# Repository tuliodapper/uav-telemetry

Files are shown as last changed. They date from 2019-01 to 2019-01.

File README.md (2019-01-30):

# uav-telemetry
The purpose of this work is to provide a cost-effective method to gather important information of a flight for project validation. Because some of the data need to be gathered at a particular condition, it is desirable that the flight is constantly monitored in order to help the pilot to achieve a specified condition, e.g., altitude. To sum up, this work aims to build a platform responsible for collecting airspeed, orientation and altitude of a fixed-wing UAV flight, and current drained by the radio receiver and the servo actuators. In addition, the low-cost instrumentation system should be capable of acquiring, storing and transmitting these relevant flight parameters to a ground control station.

## Folders

### doc
Contains report, articles, presentation and video.

### software
Contains MATLAB code for the control panel interface, which aims to monitor the data collected from the acquisition board and transmitted to the ground station. Use MATLAB R2015a or later versions.

### firmware
Contains Arduino code and libraries for the firmware of the acquisition board.

### hardware
Contains the board and schematic EAGLE files for the hardware of the acquisition board.

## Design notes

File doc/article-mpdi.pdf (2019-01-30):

## drones (http://www.mdpi.com/journal/drones)

Article

# Development and Testing of a Low-Cost Instrumentation Platform for Fixed-Wing UAV Performance Analysis

Tulio Dapper e Silva ID (https://orcid.org/0000-0002-4841-0418) and Vinicius Cabreira and Edison Pignaton de Freitas *

Department of Electrical Engineering, Federal University of Rio Grande do Sul, Porto Alegre, RS 90035-190, Brazil; tuliodapper@gmail.com (T.D.e.S.); vinicius.cabreira@outlook.com (V.C.)
* Correspondence: edison.pignaton@ufrgs.br

Received: 22 April 2018; Accepted: 17 May 2018; Published: 21 May 2018

(http://www.mdpi.com/2504-446X/2/2/19?type=check_update&version=1)

Abstract: The flight data of a fixed-wing Unmanned Aerial Vehicle (UAV) can be evaluated by its designers in order to analyze its performance, to validate the project criteria and to make new decisions based on the data analyses. In this paper, the authors propose the development of a low-cost instrumentation platform capable of collecting the following data: airspeed, orientation and altitude of the airplane, and the current drained by the electric system. Moreover, this paper presents the use of a telemetry system in order to display the flight conditions to the pilot. The system contains a variety of sensors, which were chosen based on their price, applicability and ease of use. After a test flight had been performed, the collected measurements were plotted and analyzed. Having the flight data, a set of flight characteristics might be observed.

Keywords: Unmanned Aerial Vehicle; instrumentation; telemetry; flight data

### 1. Introduction

The design of an aircraft is a challenging process that requires intelligent use of aerodynamic knowledge and involves making a large number of decisions [1]. Ground-based methods, such as wind tunnels, simulators and software models, although useful, are limited in their ability to fully model the dynamic and true nature of an actual flight [2]. Moreover, Stoliker [2] points out that flight test data are essential to both improve and validate the accuracy of models and simulations.
The purpose of this work is to provide a cost-effective method to gather important information of a flight for project validation. Because some of the data need to be gathered at a particular condition, it is desirable that the flight is constantly monitored in order to help the pilot to achieve a specified condition, e.g., altitude. In addition, this study is focused on providing an affordable tool for students participating in SAE AeroDesign competition [3].
Roskam and Lan [4] and Ojha [5] point out that the airspeed, orientation, and altitude are fundamental information in order to analyze critical conditions of a flight. In a UAV, the current drained by the electric system is important to specify battery and wire sizes. Further, the current measurement could also be used to trace a relation between the torque applied to a servo and the flight control surface attached to it. To sum up, this work aims to build a platform responsible for collecting airspeed, orientation and altitude of a fixed-wing UAV flight, and current drained by the radio receiver and the servo actuators. In addition, the low-cost instrumentation system should be capable of acquiring, storing and transmitting these relevant flight parameters to a ground control station. Besides this introduction, the paper is structured as follows: Section 2 presents some related works to this paper. Section 3 discusses the requirements for each measurement. Section 4 presents the conception of the instrumentation systems, reviewing important concepts used in its development.
Drones 2018, 2, 19; doi:10.3390/drones2020019 (http://dx.doi.org/10.3390/drones2020019) | www.mdpi.com/journal/drones

Drones 2018, 2, 19 | 2 of 14

Section 5 describes and discusses the acquired results, while Section 6 concludes the paper, providing also directions for future work.

### 2. Related Works

A portable and low-cost hardware for flight testing in commercial aircraft was proposed by Kish et al. [6]. The developed instrumentation system was capable of collecting airspeed, pressure, altitude, and ambient temperature, among other measurements. The authors considered that the platform has shown promising potential to perform flight test measurements and would be useful as a primary flight reference system for home-built aircraft.
An instrumentation system might be needed for many applications and rather exclusively aircraft’s projects evaluation. For instance, Kugler and Holzapfel [7] proposed the use of flight data for implementing automatic take-off maneuver for a fixed-wing UAV and Lesprier et al. [8] presented a robust nonlinear control of a fixed-wing UAV. Moreover, Bryson and Sukkarieh [9] described the use of this information for building large-scale 3D terrain reconstructions.
In order to collect, process and store important flight data, Rodriguez et al. [10] presented an acquisition platform for experimental UAV research. The proposal was collecting UAV’s flight data (e.g., airspeed, ground speed, position, altitude, angle of attack and sideslip) focused on providing accurate and synchronized timestamps to all measurements. Complementary to those studies analyzed above, other studies (see for example [11–14]) described alternative methods of estimating attitude and position during a UAV’s flight performing data fusion algorithms.

### 3. Project Requirements’ Specification

As a starting point for this proposed work, a study about the target UAV platform was performed. Based on this study, the requirements for the desired instrumentation systems were defined. The fixed-wing UAV named “JF-01”, developed by Pampa AeroDesign UFRGS, was taken as a reference platform, which is depicted in Figure 1. Then, the desired range and accuracy of each measurement was specified to facilitate the determination of the sensors and the methods to be used.

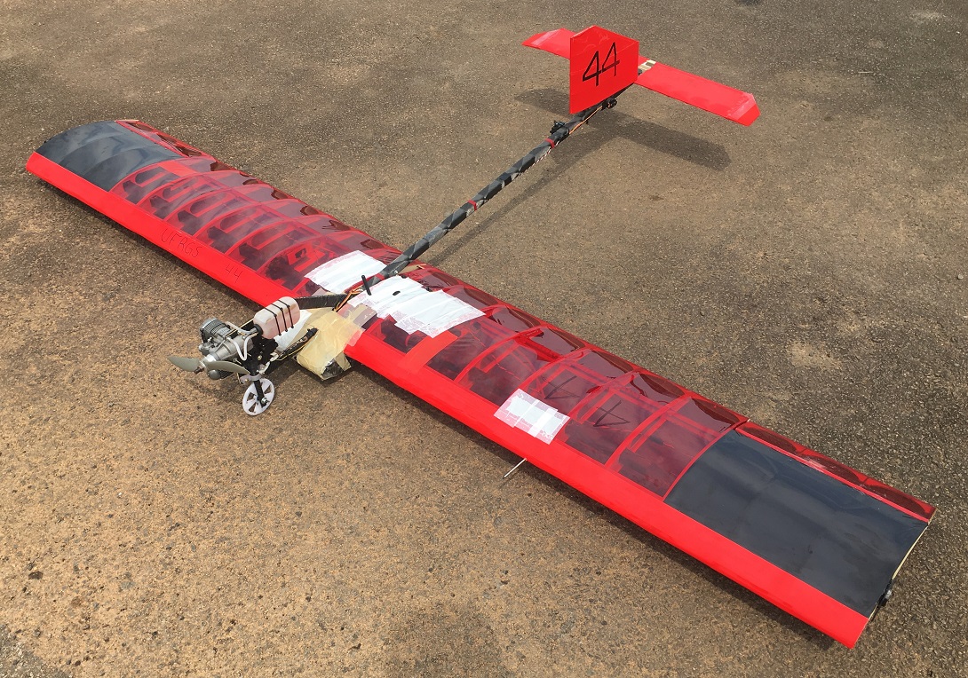
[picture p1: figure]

Figure 1. Fixed-wing UAV used as a reference to the project requirements’ specification.

Aiming to address the UAV’s requirements proposed by the SAE Aerodesign competition, the airspeed below 10 m/s is not interesting, because the airplane would not be able to carry enough load. For structural reasons, the UAV is not capable of flying over 20 m/s. Thus, the measuring range should be 10 m/s up to 20 m/s. The maximum permissible error is 0.5 m/s.
The orientation might be used to verify the rolling criteria in a fixed-wing UAV project. The JF-01 was projected to reach 30o
in 0.7 s. In order to collect at least 10 points of this movement, the sample period needs to be up to 70 ms. The maximum permissible error is 1.5o

In the flight testing location, the altitude reached by the UAV would not pass 300 m above sea level. For this measurement, the maximum permissible error is 0.5 m.
In addition, the platform should be able to measure the maximum current drawn by the electric system. The maximum permissible error is 50 mA.

### 4. Materials and Methods

As an overview, Figure 2 depicts the sensors considered in this work. As can be seen, there are six components attached to the main microcontroller: two of them are responsible for storing and transmitting the data, and the other four are sensors responsible for taking single measurements. In this section, each of these six components will be presented with a discussion of its choice instead of others available on the market.

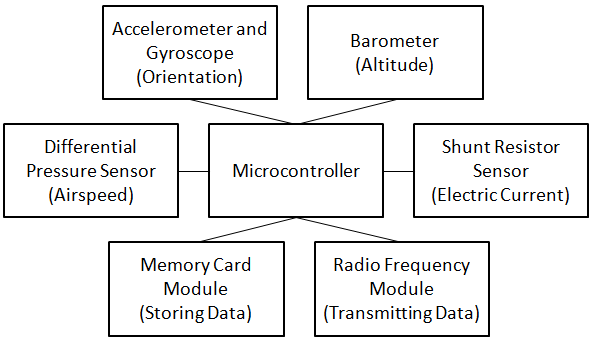
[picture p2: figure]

Figure 2. Principal components attached to the main microcontroller.

4.1. Microcontroller

In order to implement the airplane instrumentation system, an Arduino prototype platform was chosen to be used due to its low price, ease of use and ease of programming. Another important feature analyzed to decide the platform, was its size and weight, so that not too much weight had to be added to the airplane. Thus, among the available Arduino models, the Arduino Nano is a small board having similar technical specifications to the well-known Arduino Uno. Hence, the Arduino Nano was chosen.
An important parameter to be considered of the chosen platform is the quantization step size. This parameter, represented by δ, is the resolution of an analog-to-digital converter (ADC), i.e., variations in the analog signal up to δ might not cause a change in the digital value converted. The quantization step size can be calculated by the number of bits n and the full-scale voltage range

Vmax.

δ =

Vmax
2

n − 1

(1)

The ATmega328, which is the microcontroller used in Arduino Nano, contains an ADC with a resolution of 10 bits and a full-scale voltage range of 5 V. Using the Equation (1), the quantization step size δ is 0.0049 mV.

4.2. Airspeed

Nowadays, airspeed measurement is performed using a Pitot tube. In this instrument, two pressure measurements are taken through flat holes: one is facing into the fluid flow, called stagnation pressure, and other is perpendicular to the direction of fluid flow, called static pressure [5]. The dynamic pressure, which is the difference between the stagnation pressure and the static pressure, can be finally used to determine the airspeed of an aircraft.
For the measurement of the differential pressure, some sensors were searched in the market. The sensor MPX7002DP, manufactured by Freescale, is a passive element which takes two pressure measurements and converts the difference from −2 kPa up to 2 kPa to an output from 0.5 V up to 4.5 V. Having that, the sensitivity of the sensor is 1 V/kPa and the desired measurement range, in pressure terms, is from 0 Pa up to 245 Pa, then the desired measurement range, in voltage terms, is from 2.5 V up to 2.8 V.
Having the quantization step size δ, the ADC values can be evaluated. Due to the quadratic relation between the differential pressure and the airspeed, the greater the airspeed, the smaller the difference between two digital values, i.e., the resolution. The Figure 3 depicts the measurement resolution per division in function of the real airspeed. As can be seen, having the real airspeed up to

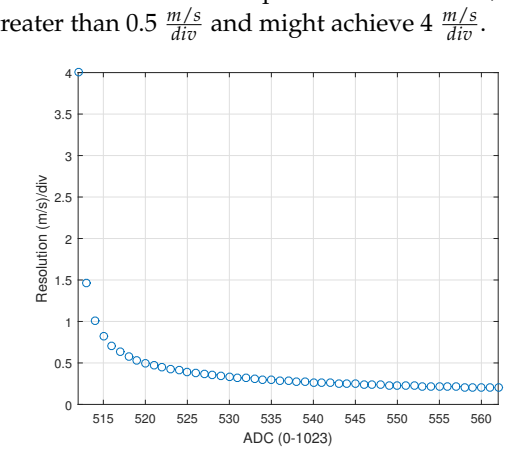
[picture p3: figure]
div and might achieve 4 m/s div .; ADC (0-1023); Resolution (m/s)/div

8 m/s, the resolution is greater than 0.5 m/s

Figure 3. Resolution of the airspeed measurement using the sensor MPXV7002DP and microcontroller ATmega328.

The component MPXV7002DP is a low-cost differential pressure sensor which is easily found in the market. However, the manufacturer points out that the measurement error might achieve 6.5%, equivalent to 250 Pa, when the offset is not adjusted. Performing this adjustment and guaranteeing temperature lower than 5

◦C, the maximum measurement error reduces to 2.5%, equivalent to 100 Pa. Considering a measurement error of 2.5% and real airspeed value of 8 m/s, the sensor might still indicate a measurement error up to 7 m/s.
The differential pressure sensor 4515DO-DS3BK002DPL, manufactured by TE Connectivity, is commonly chosen to be used in recent flight controller boards, replacing the MPXV7002DP. That sensor provides a range from 0 Pa up to 500 Pa, having greater sensibility than the low-cost mentioned. Others sensor, such as the SDP510, manufactured by Sensirion, and the LMIS500BB3S, manufactured by First-Sensor, are also indicated, due to their reliability and 0–500 Pa range. All those mentioned sensors are more expensive than the MPXV7002DP. For that reason, a set of experiments were performed using the MPXV7002DP, in order to evaluate repeatability and accuracy of the sensor measurements. Experiments were performed in order to evaluate the MPX7002DP responses. As a reference instrument, a Pitot tube attached to a differential pressure manometer was used. The Pitot tube attached to the sensor and the Pitot tube for reference measurements were placed side-by-side, as shown in Figure 4a. The differential pressure manometer presented in Figure 4b already has airspeed marks used as reference values for the calibration of the MPX7002DP.
The Figure 5a depicts the 2th-order calibration curve drawn based on 30 points collected from 8 m/s up to 16 m/s. In order to test the sensor repeatability, i.e., the capability of providing responses closed to each other, five measurements airspeed were taken for each reference value. For each set of measurements, the mean and standard deviation where calculated. Thus, the confidence interval on the mean based on 95% confidence interval, using a t-Student distribution, was performed. The Figure 5b depicts the analysis in which dots represents the population mean and the lines represent the confidence interval on the mean.

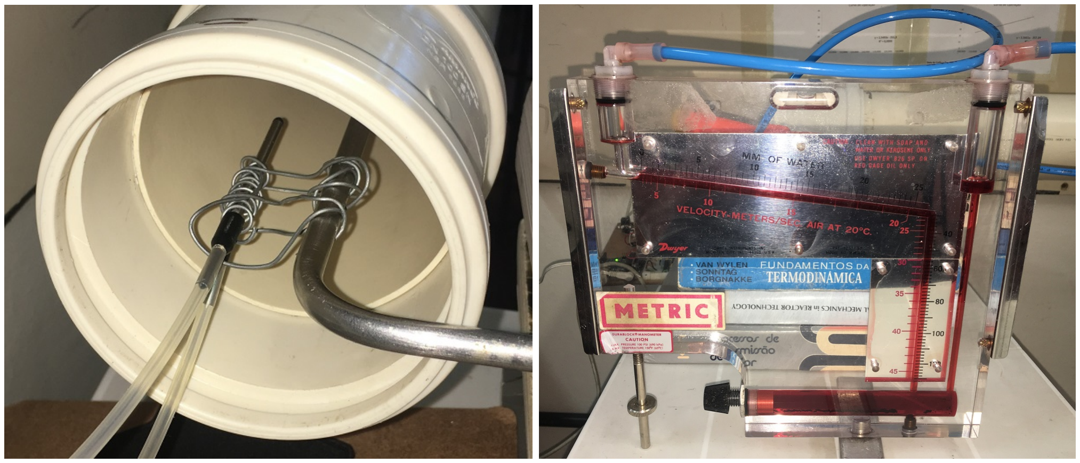
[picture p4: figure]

(a) (b)

Figure 4. (a) Pitot tube (in the left) attached to the MPX7002DP differential pressure sensor. Pitot tube (in the right) attached to the differential pressure manometer used as reference. (b) Differential pressure manometer based on fluid mechanisms having airspeed marks.

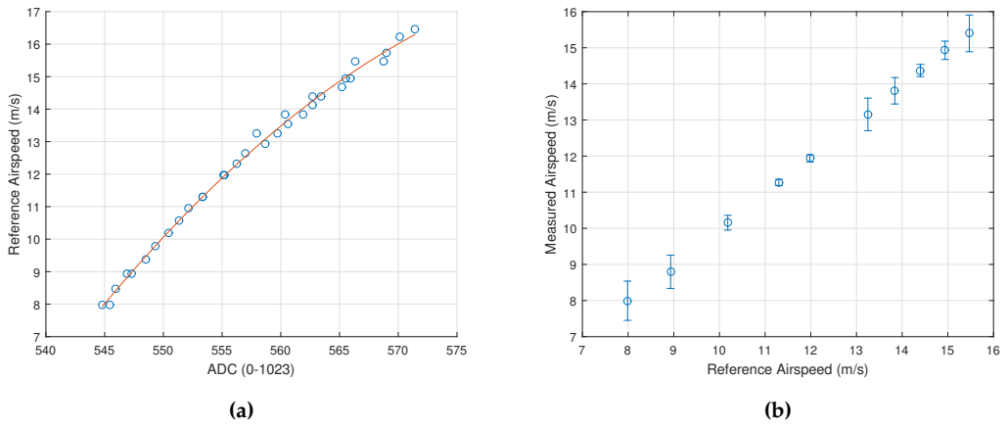
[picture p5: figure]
ADC (0-1023); Reference Airspeed (m/s); Measured Airspeed (m/s)

Figure 5. (a) Calibration curve of the airspeed measurement using the sensor MPXV7002DP and microcontroller ATmega328. (b) Confidence interval on the mean based on 95% confidence interval, using a t-Student distribution.

As can be seen in Figure 5b, the instrument response is acceptable in terms of measurement repeatability. The values did not pass through 0.5 m/s considering 95% confidence interval. Moreover, the instrument resulted in a great accuracy capability, as a result of the mean values being closed to the reference.

4.3. Orientation and Altitude

Readings of an accelerometer and a gyroscope are essential for determining the UAV orientation. Barometric pressure sensing is fundamental for having the altitude data. In the market, the following components were found in order to obtain these measurements: GY-80, GY-87, and GY-91. The Table 1 shows the sensors contained in each model.
One of the pros of the GY-87 and the GY-91 is their sensor specification of acceleration and angular speed. The MPU6050 contains an internal processor able to estimate position without the need for external data processing.
The barometers of the three models are able to measure from 300 hPa up to 1100 hPa, equivalent to 9000 m and −500 m related to ground. According to the manufacturer, the BMP085 might have a maximum measuring error of 0.5 hPa, equivalent to 4 m. The BMP180 and the BMP280 are better than the other, having a maximum measuring error of 0.12 hPa, equivalent to 0.5 m.

Table 1. Sensors contained in each module.

| GY-80 | GY-87 | GY-91
Accelerometer | ADXL345 | MPU6050 | MPU6500
Gyroscope | L3G4200D | MPU6050 | MPU6500
Magnetometer | HMC5883L | HMC5883L | AK8963
Barometer | BMP085 | BMP180 | BMP280

Due to the pressure sensor specification, price, market availability and the internal processor of the MPU6050, the GY-87 was selected to be used in this work. In order to collect orientation data, the authors used the open-source library published by Rowberg [15]. This library facilitates the acquisition of the orientation information by establishing a communication with the internal processor contained in the MPU6050.

4.4. Electric Current

In order to obtain the electric current measurement needed for this application, two types of sensors were taken into account. One of them is based on the Hall effect to find the current passing through it and the other one has a shunt resistor as the sensor.
The ACS712-ELCTR-05B-T is an electric current sensor, which uses the Hall effect in order to measure from −5 A up to 5 A with a sensibility of 185 mV/A. Having the quantization step size of 0.0049 mV, the resolution is 27.22 mA/div. Considering the manufacturer specification, the sensor might have a maximum absolute error of 1.5% of full scale.
A second option would be using a measurement instrument which uses a shunt resistor as the sensor. The chip INA219 measures the electric voltage in the resistor, realizes the analog-digital conversion, converts to electric current unit and transmits that value using I2C protocol. The range of this sensor is from −3 A up to 3 A and the quantization step size is 10 µV. According to the manufacturer, the maximum absolute error is 0.5% of full scale, equivalent to 16 mA.
The time needed to perform the reading using the IC INA219 is longer than performing an A/D conversion using the ACS712. In addition, the INA219 is more expensive than the ACS712. However, the INA219 is an instrument which is already calibrated from the manufacturer. For that reason, this sensor was chosen.
4.5. Radio Frequency Module

As mentioned in Section 1, there is a need for establishing a communication between the instrumentation platform and a ground station. A MATLAB interface was developed in order to display the flight data and send a set of user commands to the platform. This linkage will be established through radio frequency modules. In this section, two modules are presented: one is manufactured by XBee and the other by 3DR.
The XBee radios are radio frequency modules which use ZigBee protocol in order to communicate themselves using the industrial, scientific and medical (ISM) radio bands. Due to the ZigBee protocol, the communication is well-established, protected against external interferences, and allows more than 64,000 devices attached.
The manufacturer 3DR offers low-cost radio frequency modules. The company uses the open-source firmware SiK developed by ArduPilot [16]. As a consequence, the communication is supported with a message corrector (able to reconstruct 25% of defective bits) and uses the concept of Frequency-Hopping Spread Spectrum (FHSS). The FHSS is a method of transmitting signals that changes the carrier among many frequency channels. As a consequence, the communication is also highly resistant to external interferences.

In this work, there is no need for multiple devices. Furthermore, the price for the acquisition of an XBee device is considerably greater than a package of transmitter and receiver from the manufacturer 3DR. Thus, the 3DR radio frequency modules were chosen to be used.
According to the manufacturer 3DR, the voltage source for the modules must be able to provide from 3.7 V to 6 V and up to 500 mA. The Arduino Nano contains the IC AMS1117 as the voltage regulator, which is able to provide up to 800 mA. Considering the fact that the voltage regulator contained in the Arduino Nano has to be able to power the internal circuit and all other components in the acquisition board, then a dedicated voltage regulator circuit for the RF module was developed. In this circuit, the low-cost chip LM7805 was used. This IC should be powered by a 7–20 V power source and can provide from 4.75 V up to 5.25 V and up to 1 A.
4.6. Data Acquisition Board

A data acquisition board was built in order to integrate the selected components which were presented in the previous sections. The Figure A1 contains the electric diagram developed in order to design a PCB layout, having the items listed in Table 2. The Figure 6 presents the built data acquisition board. In this figure, the components are indicated through the legends of Table 2.

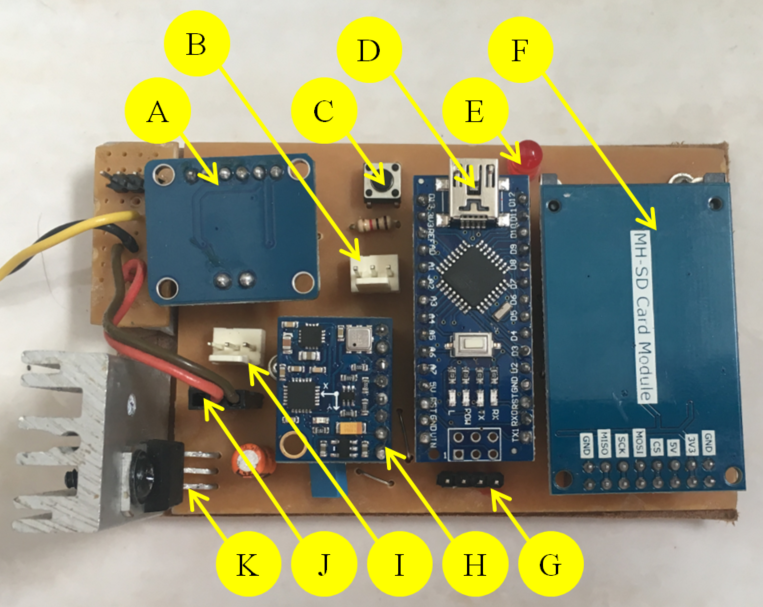
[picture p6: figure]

Figure 6. Data Acquisition Board.

Table 2. List of components included in PAD.

Legend | Component
A | Electric Current Sensor (INA219)
B | Conector for Differential Pressure Sensor (MPX7002DP)
C | Auxiliar Button
D | Arduino Nano
E | Sinalization LED
F | SD Card Reader and Writter Module
G | Conector for Radio Frequence Module
H | Module GY-87 (BMP180 and MPU6050)
I | Conector for Measuring Electric Current
J | Conector for Power Supply
K | Voltage Regulator for Radio Frequency Module
4.7. Communication Protocol

The devices chosen to be used in this work use different sorts of communication standards. Among them, there are the UART protocol, SPI, and I2C.

The UART protocol is an asynchronous serial communication. In the case of non-use of the flow control, the communication is established using two unidirectional channels: one for transmitting and other for receiving data, called TX and RX.
The SPI protocol is a synchronous serial communication. As a consequence, there is a dedicated channel to the clock signal in order to provide the synchronism in all the devices. The SPI communication uses the Master-Slave concept, in which the Master is able to select the Slave through the SS channel. For that reason, the Master must have a dedicated digital output for each Slave attached to the network. In addition, there are the MOSI and MISO channels. They are bi-directional channels responsible for transmitting data in Master-Slave and Slave-Master direction. In this work, the SPI protocol is used to store the data on the memory card. The library SdFat published by Greiman [17] was used in order to perform the communication task.
Similar to the SPI protocol, the I2C protocol is a synchronous serial communication based on the Master-Slave concept. In order to establish the communication, the SDA and SCL channels are used. Through the SCL channel, the Master is capable of setting the clock. Through the SDA channel, the data is transmitted in Master-Slave and Slave-Master direction. In order to be able of sharing a same data transmission channel, the devices are identified with an individual address. The I2C protocol is used by the microcontroller to communicate with the BMP180, the MPU6050, and the INA219. For each of them, there is a specific library being used: the BMP180 published by Sminghub [18], the Adafruit-INA219 published by Adafruit [19] and the Wire which belongs to the Arduino’s native library.
4.8. Data Acquisition Firmware

A firmware contains a sequence of routines implemented in a microcontroller aimed to perform a set of tasks demanded by an application. The Table 3 presents the main tasks needed for the present work, as well as the time needed for each of them.

Table 3. Time of tasks performing

Task | Time (µs)
Readings of Pitch and Roll from MPU6050 | 784
Readings of Differential Pressure from MPX7002DP | 116
Readings of Absolute Pressure from BMP180 | 15,428
Readings of Electric Current from INA219 | 2032
Storing Data on a SD Card | 3032
Transmitting Data through RF | 1744
Creating a new file on a SD Card | 512,100
Closing a file on a SD Card | 22,792

Firstly in the firmware sequence, the setup of the variable and the initialization of the components attached to the microcontroller is performed. Soon after, the acquisition and transmission of the data are started. The system erases the memory card and creates a fixed number of files. In the next iterations, the system collects the sensors information, transmits all the gathered data to a ground station and store these data on a memory card. The transmission and storage of the data occur at 15 Hz. The Figure A2 presents a flowchart describing in detail the sequence implemented.

4.9. Installing the Components in a Fixed-Wing UAV

In order to have the Pitot tube positioned in a fixed-wing UAV, studies in flow dynamics around an airfoil were performed. The Figure 7 depicts the pressure field distribution around a generic airfoil. As can be seen, the pressure varies according to the flow compressibility during its movement. Actually, the difference between the atmospheric pressure and the altered pressure provide the acceleration or the deceleration of the air around the airfoil.

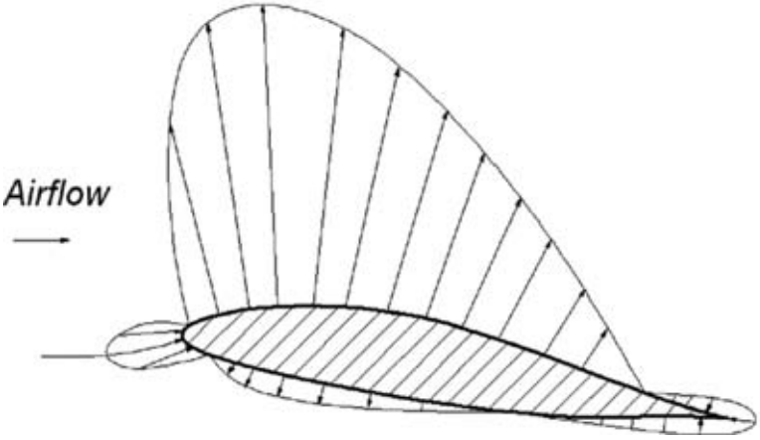
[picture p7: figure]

Figure 7. Pressure field distribution around a generic airfoil [1].

As a result of the pressure field distribution around a generic airfoil shown in Figure 7, the best position for the Pitot tube would be ahead and under the leading edge. However, the fixed-wing UAV used in the test is a low wing aircraft, at 7 cm to the ground. For that reason, the Pitot tube was placed ahead of the leading edge, in order to reduce the influence of the airflow around the wing, and avoid its impact with the ground. Moreover, the Pitot tube was placed as far as possible from the wing root in order to avoid the influence of the motor in the air flow. The Pitot tube can be seen in Figure 8.

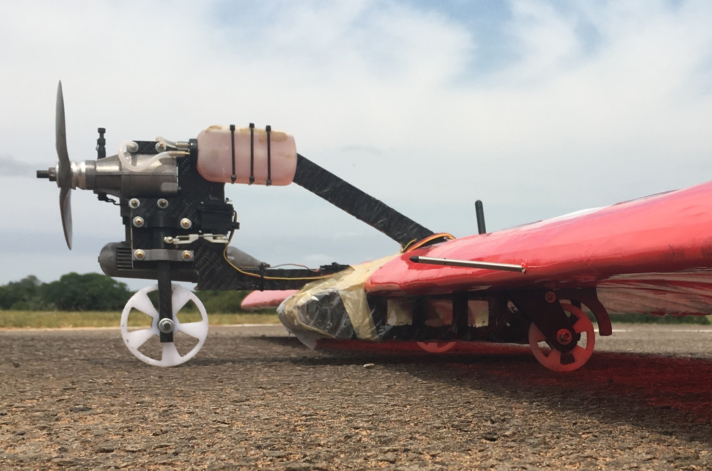
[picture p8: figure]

Figure 8. The fixed-wing UAV used for testing with a Pitot tube installed ahead of the leading edge.

### 5. Results and Discussion

Figures 9a,b present the graphs corresponding to the aircraft airspeed and altitude, respectively, during take off. A moving average using three values was performed before plotting these results. This filter was considered adequate to the response time of the system, as it is the mean from the last approximate 130 ms.
As shown in Figure 9a, the data present an oscillatory behavior between 345 s and 347.5 s. This can be explained by the structural vibration during takeoff, whilst the aircraft is still in contact with the ground. As a consequence, the effective takeoff occurs at 347.5 s. At this point in time, a slight increase in altitude and airspeed occurs, when there is no friction between the landing gears and the ground. Even though the instrument measurement of 6 m/s is out of the calibrated range between 8 and 15.5 m/s, the results are matching to the expected airspeed estimated during its project phase.
In Figure 9b, the measurement of the altitude can be evaluated. As can be seen, the instrument measured 2 m below the ground at time stand of 347.5 s. At this point, the absolute error passes over the desired maximum error of 0.5 m. From this point forward, the aircraft altitude is consistent with the flight, even though the measuring is not in accord with the work objectives.
Figures 10a,b show the values of roll angle and pitch angle, respectively, during takeoff. As can be seen in Figure 10a, the roll angle variations increases after take off, since the aircraft is no longer supported by the landing gear, being capable of maneuvering and being affected by gust winds.

Even though the aircraft is designed to have a fast rolling response, it proved higher than expected, possibly due to the low payload used during the test flight.

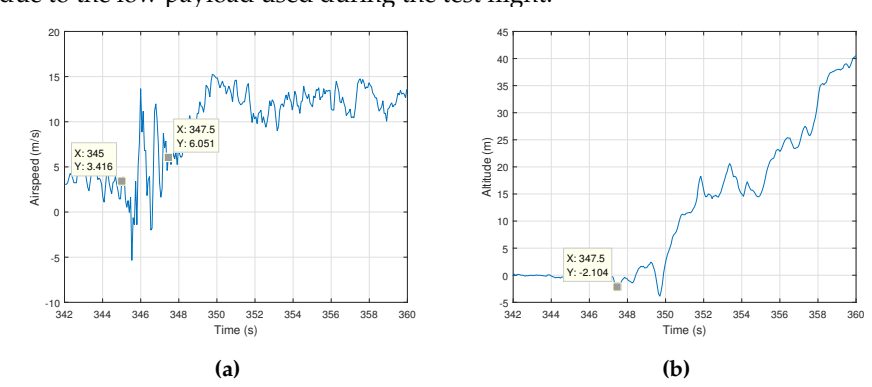
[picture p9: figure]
Time (s); Airspeed (m/s); Altitude (m)

Figure 9. (a) Airspeed of the fixed-wing UAV during the takeoff. (b) Altitude of the fixed-wing UAV

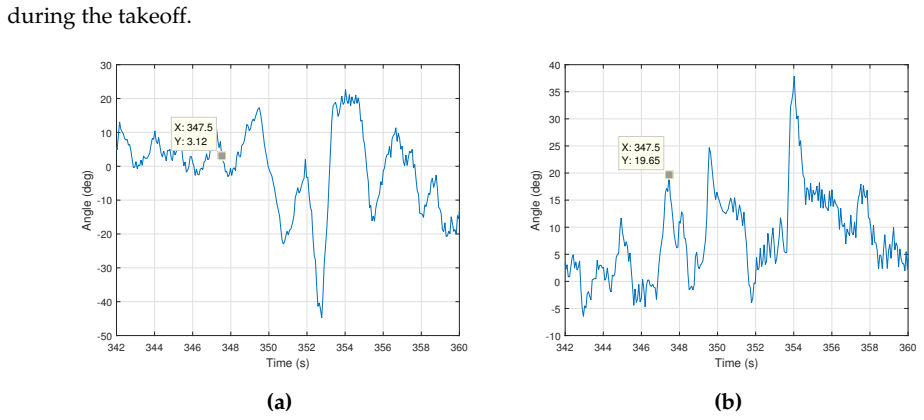
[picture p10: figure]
during the takeoff.; Time (s); Angle (deg)

Figure 10. (a) Roll angle of the fixed-wing UAV during the takeoff. (b) Pitch angle of the fixed-wing
UAV during the takeoff.

The pitch angle response during flight test, shown in Figure 10b, allows the analysis of the aircraft response to horizontal stabilizer deflection, as well as the aircraft’s pitch stability. Soon after the takeoff, a sharp increase in pitch angle can be noted, followed by a slow decrease. In parallel, a slight decrease in airspeed and an increase in altitude occurs, as expected from an ascent maneuver. This can also be noted from 352 s forward, when the aircraft holds a stable positive pitch angle, gaining altitude at a constant speed.
Using the electric current sensor INA219 installed between the battery and the electrical system, the Figure 11 shows the electric current provided by the battery. The results presented in the graph shows that the electric current drained is up to 1.5 A.

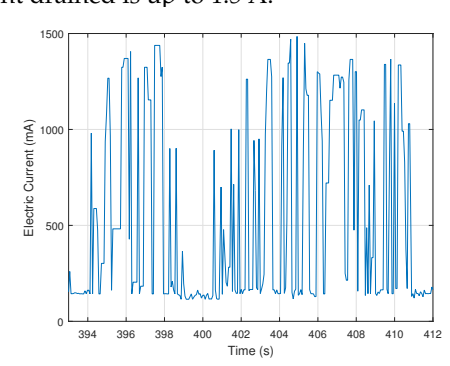
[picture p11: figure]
Time (s); Electric Current (mA)

Figure 11. Electric current provided by the battery during the flight.

### 6. Conclusions

The developed platform performed extremely well, not presenting any problems in recording or transmission of the data. The data acquired allows analyzing quantitatively and qualitatively the aircraft’s performance during the flight test. However, a few concerns and suggestions should be presented in order to guide possible future work.
There is a considerable influence of engine vibration on the data acquired. The aircraft structure and, therefore, the Pitot tube, is under mechanical vibrations generated by the engine’s rotation, which varies from 58 to 210 Hz. In order to analyze signals of frequencies lower than 210 Hz, a test is proposed in order to acquire the differential pressure sensor’s signal at a frequency higher than 420 Hz. This test would allow the identification of noises, so a proper filtering system could be developed to attenuate it. In order to perform this test, the sample rate can be increased using a data buffer. The authors suggest that a remote signal from the user should start the acquisition of samples for a fixed period and, after finishing, the data should be stored on the memory card.
After the vibration test, the authors suggest that an analog filter should be included in the sensor’s response. Digital filters could also be used, but only if the sampling frequency is twice as the filter’s cutoff frequency. Moreover, the sensor’s manufacturer suggests that a moving average should be applied with at least eight samples, reducing random errors.
Future studies are proposed to study the influence of temperature in the differential pressure sensor MPX7002DP. The maximum measuring error is established by the manufacturer considering variations of 5

◦C. Knowledge of the temperatures’ influence would enable further systematic error reduction, increasing the sensor’s accuracy.
The Pitot tube positioning can also cause variances in the sensor’s response due to the influence of the aircraft’s structure in the air flow. The authors suggest a new experiment in a wind test tunnel with the Pitot tube installed in a wing. This would allow a comparison between the sensor’s response with and without the wing’s aerodynamic influence.
In order to analyze the error in orientation and altitude, the authors propose the use of a commercial flight controller to have reference measurements. The use of these data would allow the comparison of the results and the determination of the maximum error obtained by the developed platform.

Author Contributions: Conceptualization, T.D.S. and E.P.d.F.; Formal analysis, T.D.S.; Methodology, T.D.S.; Software, T.D.S.; Validation, T.D.S. and V.C.; Visualization, T.D.S.; Writing–original draft, T.D.S.; Writing–review & editing, T.D.S., E.P.d.F. and V.C.

Acknowledgments: The authors thank the financial support by the Brazilian Research Support Agencies CAPES and CNPq to develop this work. In addition, the authors thank the members of the team Pampa AeroDesign UFRGS who provided expertise that greatly assisted the research and flight time in a fixed-wing UAV.

Conflicts of Interest: The authors declare no conflict of interest.

Abbreviations

The following abbreviations are used in this manuscript:

ADC | Analog-to-digital converter
FHSS | Frequency-Hopping Spread Spectrum
I2C | Inter-Integrated Circuit
IC | Integrated Circuit
ISM | Industrial, Scientific and Medical
MDPI | Multidisciplinary Digital Publishing Institute
MISO | Master Input Slave Output
MOSI | Master Output Slave Input
SCL | Serial Clock
SDA | Serial Data
SPI | Serial Peripheral Interface
SS | Slave Select
UART | Universal Asynchronous Receiver-Transmitter
UAV | Unmanned aerial vehicle

Appendix A

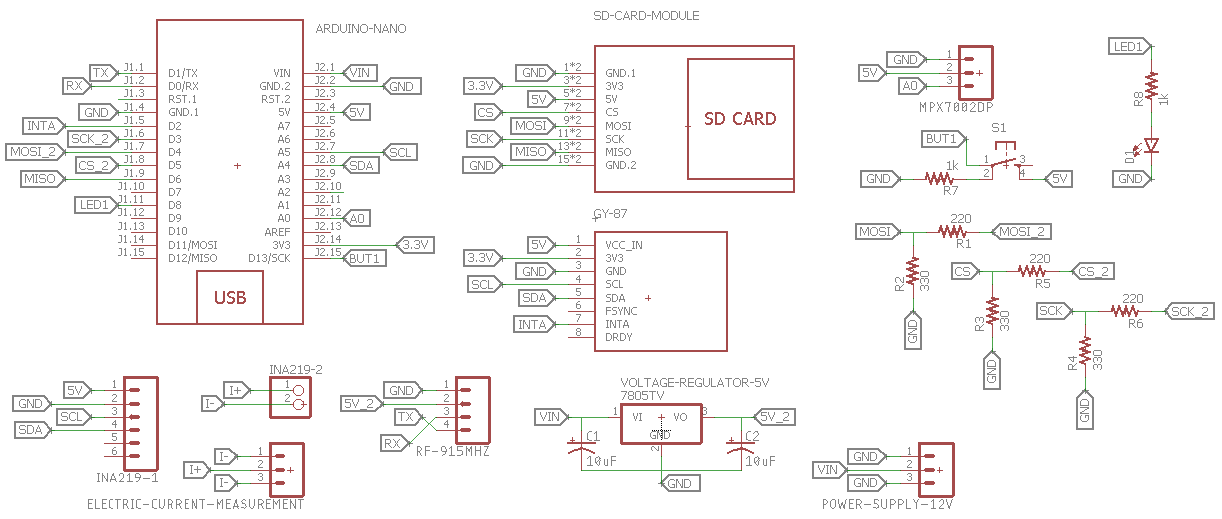
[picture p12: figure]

Figure A1. Electric Diagram of the Data Acquisition Board.

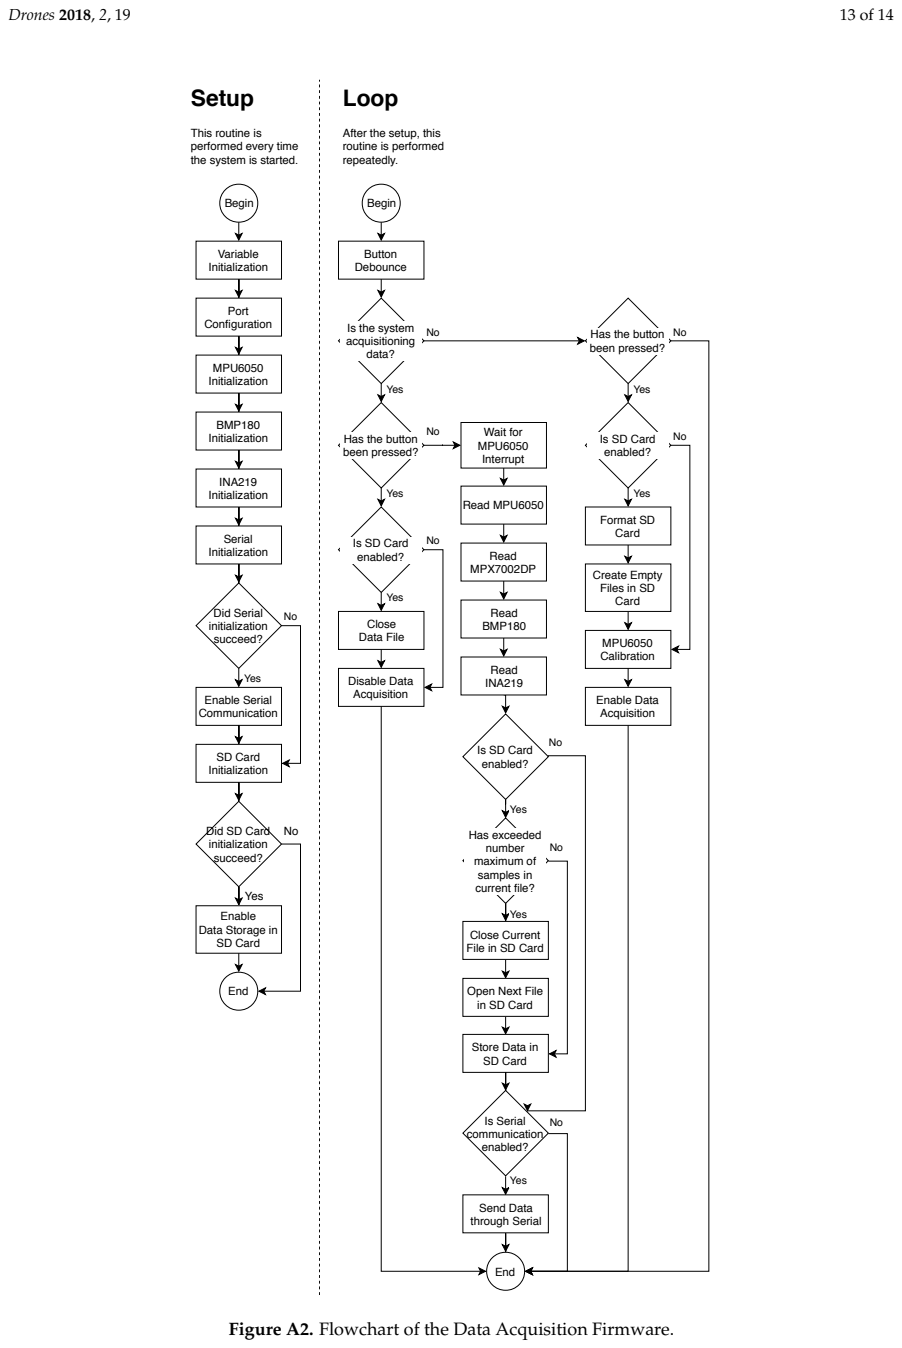
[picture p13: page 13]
Begin; Variable Initialization; Port Configuration; MPU6050 Initialization; BMP180 Initialization; INA219 Initialization; Serial Initialization; Yes; Did Serial; initialization succeed?; Enable Serial Communication; SD Card Initialization; End; Setup; Loop; Button Debounce; Close Data File; Disable Data Acquisition; Wait for MPU6050 Interrupt; Read MPU6050; Read MPX7002DP; Read BMP180; Read INA219; Has exceeded number maximum of samples in current file?; Is Serial; communication enabled?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

This routine is
performed every time
the system is started.

After the setup, this
routine is performed
repeatedly.

No Is the system
acquisitioning
data?

Has the button No
been pressed?

No Has the button

Create Empty
Files in SD
Card

Is SD Card
enabled?

Did SD Card No
initialization
succeed?

Yes
Enable
Data Storage in
SD Card

Close Current
File in SD Card

Open Next File
in SD Card

Store Data in

Figure A2. Flowchart of the Data Acquisition Firmware.

References

1. Kundu, A.K. Aircraft Design. In Aircraft Design; Shyy, W., Rycroft, M.J., Eds.; Cambridge University Press: New York, NY, USA, 2010; p. i.
2. Stoliker, F.N. Pre-Flight Tests. In Introduction to Flight Test Engineering; RTO/NATO: Neuilly-sur-Seine, France, 2005; Volume 14, p. 5.
3. International, S. SAE for Students. Available online: https://www.sae.org/students/ (accessed on 11 March 2018).
4. Roskam, J.; Lan, C.T.E. Maneuvering and the Flight Envelope. In Airplane Aerodynamics and Performance; DARcorporation: Lawrence, KS, USA, 1997; pp. 581–585.
5. Ojha, S.K. Altitudes, Airspeeds, and Wind Speeds. In Flight Performance of Aircraft; Przemieniecki, J.S., Ed.; American Institute of Aeronautics and Astronautics: Washington, DC, USA, 1995; pp. 175–185.
6. Kish, B.A.; Rhoney, M.; Kimberlin, R.D.; Vuckovic, K.; Attarian, E. Wing Bug: A portable, low-cost flight test instrumentation system. In Proceedings of the 2017 IEEE Aerospace Conference, Big Sky, MT, USA, 4–11 March 2017; pp. 1–8.
7. Kügler, M.E.; Holzapfel, F. Designing a safe and robust automatic take-off maneuver for a fixed-wing UAV. In Proceedings of the 2016 14th International Conference on Control, Automation, Robotics and Vision (ICARCV), Phuket, Thailand, 13–15 November 2016; pp. 1–6.
8. Lesprier, J.; Biannic, J.M.; Roos, C. Modeling and robust nonlinear control of a fixed-wing UAV. In Proceedings of the 2015 IEEE Conference on Control Applications (CCA), Sydney, Australia, 21–23 September 2015; pp. 1334–1339.
9. Bryson, M.; Sukkarieh, S. A comparison of feature and pose-based mapping using vision, inertial and GPS on a UAV. In Proceedings of the 2011 IEEE/RSJ International Conference on Intelligent Robots and Systems, San Francisco, CA, USA, 25–30 September 2011; pp. 4256–4262.
10. Rodriguez, A.L.; Parrilla, L.M.; Simon-Muela, A.; Prats, M.M.; Querejeta, C.; de Blanes, F.G. Real time sensor acquisition platform for experimental UAV research. In Proceedings of the Digital Avionics Systems Conference, Orlando, FL, USA, 23–29 October 2009; pp. 5.C.5-1–5.C.5-10.
11. Schmitz, G.; Alves, T.; Henriques, R.; Freitas, E.; El’Youssef, E. A simplified approach to motion estimation in a UAV using two filters. IFAC PapersOnLine 2016, 49, 325–330. [CrossRef] (http://dx.doi.org/10.1016/j.ifacol.2016.11.156)
12. Goncalves, E.S.; Rosa, P.F.F. Sensor fusion with cointegration analysis for IMU in a simulated fixed-wing UAV. In Proceedings of the 2017 International Conference on Military Technologies (ICMT), Brno, Czech Republic, 31 May–2 June 2017; pp. 493–499.
13. Tang, H.; Shen, Z. An attitude estimate method for fixed-wing UAV s using MEMS/GPS data fusion. In Proceedings of the 2017 First International Conference on Electronics Instrumentation Information Systems (EIIS), Harbin, China, 3–5 June 2017; pp. 1–5.
14. Marantos, P.; Koveos, Y.; Kyriakopoulos, K.J. UAV State Estimation Using Adaptive Complementary Filters. IEEE Trans. Control Syst. Technol. 2016, 24, 1214–1226. [CrossRef] (http://dx.doi.org/10.1109/TCST.2015.2480012)
15. Rowberg, J. MPU6050 Library Repository. Available online: https://github.com/jrowberg/i2cdevlib/tree/master/Arduino/MPU6050 (https://github.com/jrowberg/i2cdevlib/tree/master/Arduino/MPU6050) (accessed on 25 August 2017).
16. ArduPilot. SiK Library Repository. Available online: https://github.com/ArduPilot/SiK (accessed on 25 November 2017).
17. Greiman, B. SdFat Library Repository. Available online: https://github.com/greiman/SdFat (accessed on 2 October 2017).
18. Sminghub. BMP180 Library Repository. Available online: https://github.com/SmingHub/SmingRTOS/tree/master/sming/libraries/BMP180 (https://github.com/SmingHub/SmingRTOS/tree/master/sming/libraries/BMP180) (accessed on 10 May 2017).
19. Adafruit. Adafruit-INA219 Library Repository. Available online: https://github.com/adafruit/Adafruit_INA219 (https://github.com/adafruit/Adafruit_INA219) (accessed on 10 October 2017).

c 2018 by the authors. Licensee MDPI, Basel, Switzerland. This article is an open access article distributed under the terms and conditions of the Creative Commons Attribution (CC BY) license (http://creativecommons.org/licenses/by/4.0/).

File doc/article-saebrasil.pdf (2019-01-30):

P á g i n a 1 | 8

### 6 FORUM SAE BRASIL AERODESIGN 2018

# Instrumentação de um veículo aéreo não tripulado para análise de seu desempenho de voo

## Túlio Dapper e Silva

## Vinicius Cabreira

## Edison Pignaton de Freitas

Universidade Federal do Rio Grande do Sul

## RESUMO

A utilização de um dispositivo capaz de coletar as informações relevantes do voo da aeronave é crucial para a análise de sua performance de voo, a realização de validações e, até mesmo, tomada de decisões ao longo do seu projeto. Este artigo apresenta o desenvolvimento de um sistema de instrumentação de um veículo aéreo não tripulado (VANT) de asa fixa capaz de coletar as seguintes informações: velocidade em relação ao ar, altitude e orientação da aeronave, e corrente elétrica drenada pelo conjunto rádio receptor e servos. O trabalho também apresenta a implementação do sistema de telemetria. Dessa forma, durante o voo, as informações são transmitidas a um computador para acompanhamento remoto por parte do piloto ou de um auxiliar. Para a realização deste trabalho, são estudados diferentes componentes cabíveis para a aplicação, os quais foram escolhidos baseados em seu custo, sua aplicabilidade e sua facilidade de utilização. Com os resultados obtidos, foi possível caracterizar o comportamento da aeronave durante o voo. No entanto, existem aspectos a serem aprimorados para que os valores apresentados possam ser considerados confiáveis, caracterizando direções para trabalhos futuros, como a atenuação da perturbação devido a vibrações mecânicas da estrutura no resultado e a comparação das medições realizadas com um instrumento de referência.

## INTRODUÇÃO

Ensaios físicos, tais como os realizados em túneis de vento, e as simulações em ferramentas computacionais, apesar de serem necessários, são limitados em sua capacidade de modelar por completo a dinâmica de um voo real (Pavlock, 2013). A utilização de um sistema de sensoriamento em um VANT pode fornecer as principais características do voo de uma aeronave; sendo ele, assim, uma poderosa ferramenta para análise de seu projeto.

O objetivo deste trabalho é desenvolver um dispositivo capaz de realizar a coleta das informações consideradas mais importantes durante o voo da aeronave de uma equipe participante da competição SAE BRASIL AeroDesign.

Deseja-se analisar os dados para condições específicas de um voo (em determinada altitude, por exemplo); por isso, em alguns casos, é importante que, para auxiliar o piloto a atingir as condições de interesse, os dados coletados possam ser monitorados durante o voo. Por fim, com o intuito de fornecer uma ferramenta acessível para equipes da competição, objetiva-se em uma solução de baixo custo.

Os estudos apresentados por Lan e Roskam (2003) e Ojha (1995) indicam que a velocidade em relação ao ar, a orientação e a altitude são informações fundamentais para condições críticas do voo de uma aeronave. A corrente drenada pelo sistema elétrico, por sua vez, impacta nos dimensionamentos dos fios e da bateria, que devem ser apresentados no relatório entregue aos juízes da competição. Portanto, neste trabalho, será estudada a implementação da coleta dos seguintes dados: a velocidade da aeronave em relação ao ar, a orientação da aeronave, a sua altitude e a corrente fornecida pela bateria para alimentação do rádio receptor dos sinais de comando e dos servos atuadores.

Para o desenvolvimento deste trabalho, é importante que seus principais requisitos sejam estabelecidos. Para isso, como referência, foi utilizado o projeto da aeronave JF-01, desenvolvido pela equipe Pampa AeroDesign UFRGS, para a competição SAE BRASIL AeroDesign 2017.

A máxima velocidade em relação ao ar da aeronave define a carga paga máxima levada pela aeronave na competição. Analiticamente, foi determinado que, para velocidades inferiores a 10m/s, a aeronave JF-01 não decola com a carga paga mínima necessária para a equipe estar competitiva. Por questões estruturais, a velocidade da aeronave está limitada a 20m/s. Portanto, a faixa de medição necessária é de 10 a 20m/s. Ainda, a tolerância desejada pela equipe é de 5%; sendo assim, o erro máximo admissível é de 0,5m/s.

A orientação pode ser utilizada de modo a validar o critério de rolagem do projeto de uma aeronave. A JF-01 é projetada para cumprir 30º em 0,7s. Com o objetivo de obter, no mínimo, 10 pontos desse movimento, o período de amostragem deve ser,

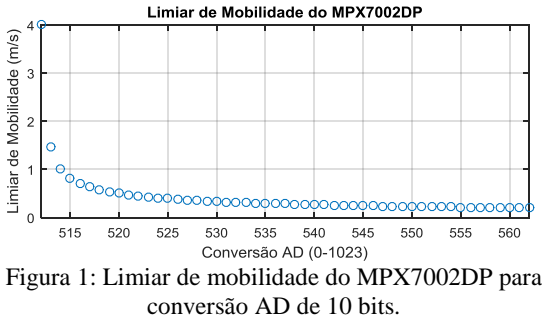
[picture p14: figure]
conversão AD de 10 bits.

P á g i n a 2 | 8

### 6 FORUM SAE BRASIL AERODESIGN 2018

no máximo, 70ms. A tolerância desejada pela equipe é de 5%; desse modo, o erro máximo tolerado é de 1,5º.

Sabe-se que, no local onde são realizados os voos, a altitude máxima atingida pela aeronave é de 300m em relação ao nível do mar. Na medição de altitude, determinou-se que a tolerância da medida é de 0,167%, equivalente a um limite de erro admissível de 0,5m.

Também é propósito deste trabalho a medição da corrente elétrica fornecida pela bateria para o sistema elétrico da aeronave. O objetivo da medição é determinar a corrente máxima drenada pelo sistema. O erro máximo admissível é de 50mA.

## METODOLOGIA

No desenvolvimento deste trabalho, será realizado um estudo dos componentes necessários para a coleta e a transmissão dos dados da aeronave durante um voo. Em seguida, será desenvolvida uma placa de aquisição de dados e o seu firmware. Para o acompanhamento das informações durante o voo e a análise dos dados após o voo, serão elaboradas interfaces gráficas para o usuário. Por fim, serão apresentados alguns cuidados quanto à instalação dos componentes na aeronave.

### 1. Processador

Escolheu-se trabalhar com a plataforma de prototipagem eletrônica Arduino, devido a sua facilidade de programação e instalação. O Arduino Nano possui especificação técnica semelhante ao Arduino Uno; contudo, o Arduino Nano é mais compacto. Por isso, adotou-se sua utilização neste trabalho.

O tamanho do passo de quantização δ é a resolução de um conversor AD. Variações no sinal analógico menores que o passo de quantização podem não causar alteração no valor digital convertido. O passo de quantização pode ser determinado em função da quantidade de bits n da conversão AD e a margem de entrada m do conversor, como mostra a Equação (1). δ

m n | (1)

O ATmega328, microcontrolador utilizado no Arduino Nano, possui 10 bits para a conversão AD e 5V na margem de entrada do conversor. Desse modo, o tamanho do passo de quantização δ é de 0,0049m .

### 2. Velocidade em Relação ao Ar

Em uma aeronave, a medição da velocidade do ar é atualmente realizada através da utilização de um tubo de Pitot. Nele, duas tomadas de pressão são realizadas: uma está alinhada com o fluxo de ar, chamada de pressão de estagnação pt

, e a outra
está perpendicular ao fluxo do ar, chamada de pressão estática pe

(Ojha, 1995).

Para a medição da pressão diferencial pt

-pe

, foram analisados
sensores existentes no mercado. Em termos da grandeza de pressão, a faixa de interesse está entre 0 e 245Pa.

O sensor MPX7002DP, da fabricante Freescale, é um elemento passivo que realiza duas tomadas de pressão e converte a pressão diferencial de -2kPa a 2kPa para a tensão elétrica de 0,5V a 4,5V. Sabendo que sua sensibilidade é 1V/kPa, verifica-se que, em termos da grandeza de tensão, a faixa de interesse está entre 2,5V e 2,8V, aproximadamente.

Com o tamanho do passo de quantização δ, é possível determinar o valor da conversão AD correspondente à medida de velocidade do ar. Devido à relação quadrática entre a pressão diferencial e a velocidade do ar, sabe-se que à medida que a velocidade do ar aumenta, menor é a variação de velocidade necessária para alterar o valor digital convertido. Segundo Balbinot e Brusamarello (2011), essa diferença é denominada limiar de mobilidade. Como é descrito pelos autores, esse valor corresponde à maior variação no estímulo que não produz variação detectável na resposta. O limiar de mobilidade é apresentado na Figura 1, em função do valor digital da conversão AD. Percebe-se que, para velocidades abaixo de 8m/s, o limiar de mobilidade é maior que 0,5m/s e pode chegar a 4m/s. A partir disso, determinou-se que o limite mínimo de trabalho do sensor é de 8m/s, no qual teria um erro máximo de 0,25m/s devido à conversão AD.

Figura 1: Limiar de mobilidade do MPX7002DP para

O componente MPX7002DP é um dos sensores de pressão diferencial mais baratos e fáceis de serem encontrados no

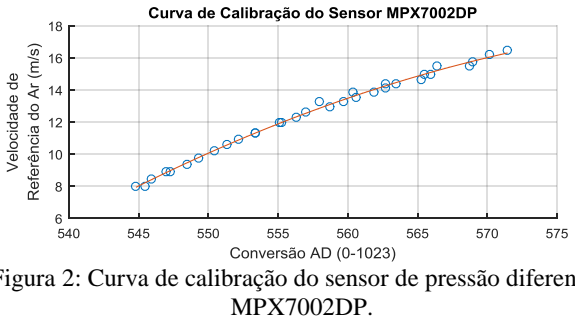
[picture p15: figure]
MPX7002DP.
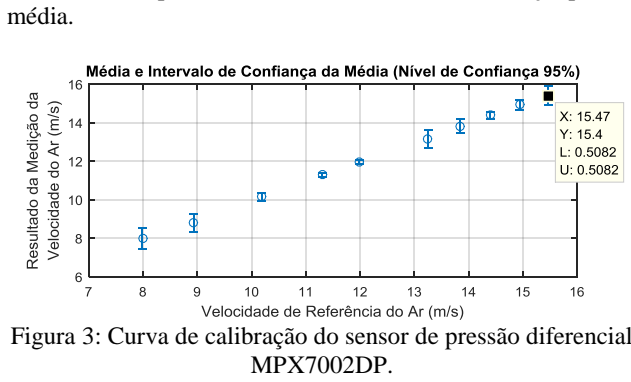
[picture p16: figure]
média.; MPX7002DP.

P á g i n a 3 | 8

### 6 FORUM SAE BRASIL AERODESIGN 2018

mercado. Porém, o fabricante indica que, sem o ajuste de offset, o erro de medição pode chegar a 6,5% da amplitude da faixa nominal, equivalente a 250Pa; se o offset for ajustado e a temperatura não variar mais que 5ºC, esse erro máximo reduz para 2,5%, equivalente a 100Pa. Considerando um erro absoluto de medição de 2,5% da amplitude da faixa nominal, para a velocidade verdadeira de 8m/s, o sistema pode apresentar erro de medição em até 7m/s devido às características construtivas do sensor.

O sensor de pressão diferencial 4515DO-DS3BK002DPL, da fabricante TE connectivity, é utilizado pelas placas
controladoras | mais | modernas, | em | substituição | ao
MPX7002DP. Sua faixa de trabalho é de 0 a 500Pa, apresentando maior sensibilidade à medição. Ainda, o sensor condiciona o sinal e transmite os dados digitalmente por meio do protocolo de comunicação I2C. Outros sensores, como o SDP610, da fabricante Sensirion, e o LMIS250BB3S da
fabricante | First-Sensor, | também | são | indicados, | pois
apresentam baixo erro de medição e a faixa de medição de ambos é de 0 a 500Pa. Todos esses sensores são mais caros e mais difíceis de serem adquiridos em comparação ao MPX7002DP; por isso, decidiu-se testá-lo, analisando sua resposta frente à repetitividade e à veracidade das medições em uma bancada de testes.

Foram realizados ensaios¹
para medição da velocidade do ar utilizando o sensor de pressão diferencial MPX7002DP e um instrumento para medição da velocidade de referência (um tubo de Pitot ligado a um manômetro de pressão diferencial por deslocamento de um fluido). Os dois tubos de Pitot estão acoplados à saída de uma tubulação, em que a velocidade do ar em seu interior pode ser controlada.

No ensaio realizado, foram coletados 30 pontos distintos de 8m/s a 16,5m/s; com isso, construiu-se a curva de calibração dada pela Figura 2. Nota-se que não foram realizadas medições para velocidades inferiores a 8m/s (devido ao erro associado ao limiar de mobilidade) e nem superiores a 16,5m/s (devido ao tempo disponível para utilização do equipamento). Cada ponto no gráfico corresponde à média de 100 amostras coletadas em intervalos de 50ms. Uma curva de segunda ordem foi utilizada para representar os pontos coletados, como pode ser visto na figura abaixo.

1
Ensaios realizados no Laboratório de Aplicações em
Energia | e | Fenômenos | de | Transporte | (LAEFT) | da
Universidade Federal do Rio Grande do Sul (UFRGS).

Figura 2: Curva de calibração do sensor de pressão diferencial

Com o objetivo de testar a repetitividade, ou seja, a aptidão do instrumento em fornecer indicações próximas entre si, cinco novos ensaios foram realizados. Sabe-se que as condições de medição eram intermediárias, podendo ter ocorrido erro na leitura visual da medida da velocidade de referência, assim como mudanças de temperatura e pressão de uma amostra para a outra. Ainda assim, determinou-se a média e o desvio padrão para 10 conjuntos de amostras coletadas no intervalo de 8 a 15,5m/s. A partir de então, foi determinado o intervalo de confiança da média considerando nível de confiança de 95% utilizando a distribuição t de Student, devido ao baixo número de amostras coletadas. A Figura 3 apresenta a análise realizada, onde os pontos representam as médias dos conjuntos e as linhas representam os intervalos de confiança para a

Figura 3: Curva de calibração do sensor de pressão diferencial

Como pode ser visto na Figura 3, os resultados obtidos no teste foram satisfatórios. Nota-se que o instrumento apresenta repetitividade de medição aceitável, já que, para o nível de confiança adotado, as medidas respeitam o erro máximo tolerável de 0,5m/s. Ainda, o sistema apresentou boa veracidade de medição, visto que as médias estão próximas às velocidades de referência. Devido ao fato de que foi validada a utilização do sensor somente no intervalo apresentado na figura, para este trabalho, determinou-se que a faixa de trabalho do instrumento é de 8 a 15,5m/s.

P á g i n a 4 | 8

### 6 FORUM SAE BRASIL AERODESIGN 2018

### 3. Orientação e Altitude

As medições de um acelerômetro e um giroscópio são essenciais para determinação da orientação da aeronave. A tomada de pressão atmosférica, por sua vez, nos fornece a altitude da aeronave. Procurou-se, no mercado, módulos que possuíssem os sensores das grandezas mencionadas. Foram encontrados três principais módulos: GY-80, GY-87 e GY-91.

Tabela 1: Sensores pertencentes a cada módulo.
GY-80 | GY-87 | GY-91
Acelerômetro | ADXL345 | MPU-6050 | MPU-6500
Giroscópio | L3G4200D | MPU-6050 | MPU-6500
Magnetrômetro | HMC5883L | HMC5883L | AK8963
Barômetro | BMP085 | BMP180 | BMP280

Uma das vantagens do GY-87 e do GY-91 é que o acelerômetro e o giroscópio contém um processador interno, que estima a orientação do componente, dispensando esse cálculo do sistema de aquisição dos dados.

Os barômetros dos três módulos trabalham em uma faixa de medição entre 300 e 1100hPa que, em termos de altitude em relação ao nível do mar, está entre 9000m e -500m. De acordo com as especificações do fabricante, o máximo erro de medição que o BMP085 pode apresentar é de 0,5hPa, equivalente a 4 metros. Para o BMP180 e o BMP280, o erro de medição pode chegar a 0,12hPa, equivalente a 1,5 metros. Para todos os sensores apresentados, portanto, o erro indicado pelo fabricante ultrapassa o limite de erro admitido de 0,5m; porém, espera-se melhorar o resultado através da média das medidas obtidas em um curto intervalo de tempo.

Devido a uma melhor especificação do sensor de pressão, ao preço, à disponibilidade no mercado e ao fato de que o MPU6050, assim como o MPU6500, possui processador interno, optou-se pelo módulo GY-87.

Acelerômetros são sensíveis a vibrações e a forças externas; os giroscópios, por sua vez, são propícios a acumular erro durante a integração. Assim, faz-se necessário a fusão dos dados dos sensores. Para a determinação do ângulo de arfagem
e | rolagem, | optou-se | pela | implementação | do | Filtro
Complementar.

### 4. Corrente Elétrica

O ACS712-ELCTR-05B-T é um sensor de corrente elétrica por efeito Hall, não invasivo, com faixa nominal entre -5A e

5A e sensibilidade de 185mV/A. Considerando o tamanho do passo de quantização de 0,0049mV, o limiar de mobilidade é de 27,22mA. Segundo as especificações do fabricante, o componente pode apresentar erro absoluto de 1,5% do fundo de escala, equivalente a 75mA.

Uma segunda opção é a utilização de um instrumento de medição que utiliza um resistor do tipo shunt como sensor. O CI INA219 condiciona a tensão elétrica medida de um resistor, realiza a conversão AD, converte o valor para a grandeza de corrente elétrica e transmite o dado através do protocolo I2C. A faixa nominal do componente é de -3,2A a 3,2A e o tamanho do passo de quantização do INA219 é de 10µV, sendo o limiar de mobilidade de 0,1mA. Ainda, segundo o fabricante, o erro máximo absoluto é de 0,5% do fundo de escala, equivalente a 16mA.

Sabe-se que o tempo de comunicação para a leitura de uma variável no barramento I2C (utilizado no INA219) é maior que o tempo de conversão AD de um sinal analógico (fornecido pelo ACS712). Também, o custo para aquisição do INA219 é maior que o do ACS712. Ainda, apesar do erro apresentado pelo fabricante do sensor ACS712 ser maior que o erro máximo tolerado para a medida, essa diferença pode ser reduzida com a realização da média de um conjunto de medidas realizadas em um curto intervalo de tempo. Contudo, devido ao fato de que o INA219 é um instrumento que já está calibrado, preferiu-se utilizá-lo.

### 5. Módulo de Rádio Frequência

Os rádios XBee são módulos de rádio frequência que utilizam o protocolo ZigBee para a comunicação entre si. Os rádios operam na frequência ISM (Industrial, Scientific and Medical), sendo essa frequência 2,4GHz no Brasil, e, devido ao protocolo utilizado, oferecem alta imunidade contra interferências e permitem hospedar milhares de dispositivos.

A fabricante 3DR oferece, por sua vez, módulos de rádio frequência com menor custo, comparado aos módulos da XBee. Em seus dispositivos, a fabricante utiliza o firmware de código aberto SiK compartilhado por ArduPilot (2017). Com a utilização desse firmware, a comunicação possui um corretor de mensagens enviadas (que corrige até 25% dos bits com defeito) e utiliza o espectro de difusão em frequência variável (Frequency-Hopping Spread Spectrum ou FHSS). O FHSS é um método que permite a mudança do sinal da portadora em vários canais de frequência; dessa forma, possui alta resistência a interferências também.

P á g i n a 5 | 8

### 6 FORUM SAE BRASIL AERODESIGN 2018

Neste trabalho, não há a necessidade de uma rede de dispositivos. Ainda, o custo para aquisição de um módulo XBee é consideravelmente superior ao do par emissor e receptor da fabricante 3DR. Assim, optou-se por utilizar os módulos de rádio frequência da fabricante 3DR. Escolheu-se, devido a disponibilidade do produto no mercado e a atribuição de faixas de frequências no Brasil (definida pelo órgão
regulamentador | ANATEL), | utilizar | os | módulos | cuja
frequência de transmissão é de 915MHz.

De acordo com as especificações do fabricante, a tensão de alimentação dos módulos deve estar entre 3,7 e 6V, sendo que eles podem consumir até 500mA da fonte de alimentação. O Arduino Nano contém o regulador de tensão AMS1117 que, segundo sua especificação, pode fornecer até 800mA. Visto que o regulador de tensão do Arduino deve alimentar o circuito interno e os demais componentes da placa, foi projetado um circuito regulador de tensão dedicado ao módulo RF da 3DR. Para isso, foi utilizado o regulador de tensão LM7805 que, a partir de uma tensão de entrada de 7 a 20V, garante de 4,75 a 5,25V em sua saída e pode fornecer até 1A.

### 6. Protocolos de Comunicação

Os dispositivos eletrônicos escolhidos nesse trabalho utilizam
diferentes | padrões | de | comunicação, | sendo | eles, | as
comunicações seriadas UART, SPI e I2C.

A comunicação UART é serial e assíncrona. Sem o controle de fluxo, como é o caso deste trabalho, a comunicação é realizada por dois canais, unidirecionais, um para transmissão e outro para recebimento dos dados, chamados de TX e RX.

Assim como a comunicação UART, o protocolo SPI também é uma comunicação seriada, porém, essa é síncrona. Portanto, há a existência de uma via para o clock, responsável por sintonizar os dispositivos, chamada de SCLK. A comunicação SPI utiliza o conceito Mestre-Escravo, onde o Mestre deve selecionar o Escravo através da via SS. Por isso, para cada dispositivo Escravo, o Mestre deve haver uma porta para a chave SS daquele dispositivo. Por fim, há os canais MOSI e MISO, que são vias unidirecionais para transmissão dos dados
na | direção | Mestre-Escravo | e | Escravo-Mestre,
respectivamente. A comunicação SPI é utilizada para a gravação dos dados no cartão de memória. De modo a facilitar a programação do firmware, foi utilizado a biblioteca SdFat desenvolvida e compartilhada por Greiman (2017).

O protocolo de comunicação I2C, por sua vez, é seriado, síncrono e utiliza o conceito Mestre-Escravo. Para a comunicação, são utilizados os barramentos SCL e SDA, que são conectados a todos os dispositivos existentes na rede. Através do canal SCL, o Mestre sincroniza o clock com os dispositivos conectados a ele. O canal SDA é responsável por transmitir os dados no sentido Mestre-Escravo e vice-versa. Para isso, todos os dispositivos possuem um endereço para que possam ser identificados na rede. O padrão I2C é utilizado para a comunicação do microprocessador com o BMP180, o MPU6050 e o INA219. Para cada um deles, utiliza-se uma biblioteca diferente, sendo elas, respectivamente: a BMP180 de SmingHub (2017), a Adafruit_INA219 de Adafruit (2017) e a Wire (biblioteca nativa do Arduino).

### 7. Firmware da Placa de Aquisição de Dados

O firmware possui uma sequência de rotinas implementada no microcontrolador de modo a executar todas as operações demandadas pela aplicação. A Tabela 2 apresenta o tempo de execução das principais rotinas a serem executadas.

Tabela 2: Tempo de execução das rotinas.

O programa é dividido em duas etapas: a primeira é denominada Setup, executada toda vez que o microcontrolador é ativado; a outra é o Loop, que se repete até que o sistema seja desligado.

Na fase de Setup, é realizada a inicialização das variáveis e a configuração inicial dos componentes. Pode ser visto no fluxograma que, após as configurações, são verificadas as presenças do cartão de memória para gravação e de um dispositivo conectado ao canal de comunicação serial. Vale ressaltar que tanto um módulo RF, quanto um computador, pode estar conectado ao canal de comunicação serial.

Assim que o sistema é configurado, através da fase de Setup, inicia-se a fase de Loop. Para dar início à coleta e à transmissão dos dados, o usuário deve apertar um botão. A

Rotina | Tempo (us)
Leitura do Acelerômetro e Giroscópio | 1872
Cálculo dos ângulos de rolamento e arfagem | 716
Leitura do Sensor de Pressão Diferencial | 116
Leitura do Sensor de Pressão | 15428
Leitura do Sensor de Corrente Elétrica | 2032
Gravação dos Dados no Cartão SD | 3032
Transmissão dos Dados por Rádio Frequência | 1744
Criação de um Arquivo no Cartão SD | 512100
Encerramento de um Arquivo no Cartão SD | 22792

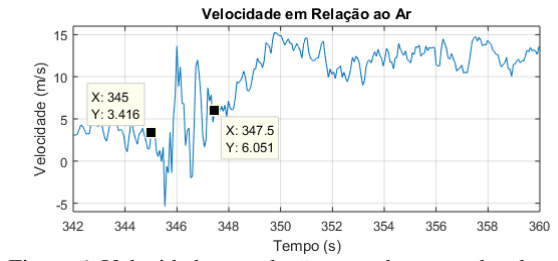
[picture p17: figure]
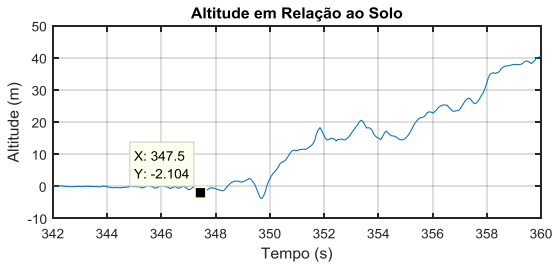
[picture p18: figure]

P á g i n a 6 | 8

### 6 FORUM SAE BRASIL AERODESIGN 2018

partir de então, o sistema apaga todos os arquivos do cartão de memória e repõe 100 novos arquivos. Nas iterações seguintes, o sistema passa, então, a coletar as informações dos sensores, transmitir os dados através do módulo RF e gravar os dados no cartão de memória. O período de amostragem utilizado para gravação no cartão de memória foi de 66ms, sendo que o cálculo de rolagem e arfagem era realizado a cada 33ms.

### 8. Instalação dos Componentes na Aeronave

Para a instalação do tubo de Pitot na aeronave, é importante a realização do estudo do comportamento do ar em um perfil de asa. Pode-se, assim, determinar o melhor ponto para a instalação do instrumento. Para isso, deve-se estar atento, principalmente, na distribuição de pressão em torno da asa. A Figura 4 apresenta a distribuição de pressão em torno de uma asa. A pressão em torno da asa é alterada devido à compressibilidade do fluido em deslocamento. A diferença entre a pressão atmosférica e a pressão alterada faz com que ocorra aceleração ou desaceleração do ar em torno da asa.

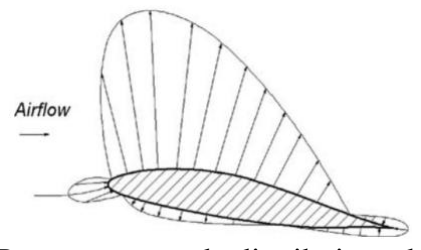
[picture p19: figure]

Figura 4: Representação da distribuição de pressão. (Kundu, 2010)

Devido à distribuição de pressão em torno da asa, o tubo de Pitot estaria melhor posicionado abaixo da asa e à sua frente. Porém, pelo fato de que a aeronave JF-01 possui asa baixa, a 7cm do solo, preferiu-se posicioná-lo à frente do bordo de ataque, de modo a reduzir sua interação com o fluxo de ar próximo a asa e, também, evitar seu contato com o solo. Outro cuidado tomado foi de posicioná-lo o mais distante possível da raiz da asa para evitar a influência do motor no fluxo de ar, como pode ser visto na Figura 5.

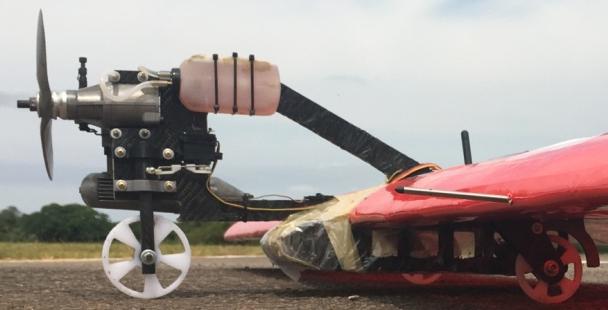
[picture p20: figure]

Figura 5: Asa da aeronave JF-01 com o tubo de Pitot instalado.

## RESULTADOS

A seguir, serão apresentadas as respostas obtidas em alguns voos realizados para teste da plataforma desenvolvida.

### 1. Velocidade em Relação ao Ar e Altitude em Relação ao Solo

A Figura 6 e a Figura 7 apresentam os gráficos correspondentes à velocidade em relação ao ar e à altitude em relação ao solo, respectivamente, durante a decolagem da aeronave. Nos gráficos, realizou-se a média móvel de três valores consecutivos, considerado adequado ao tempo de resposta desejado, pois é a média dos dados nos últimos 130ms, aproximadamente.

Figura 6: Velocidade em relação ao ar durante a decolagem.

Como pode ser visto na Figura 6, entre 345s e 347,5s, a resposta possui um comportamento oscilatório com alta amplitude. Isso pode ser explicado pela vibração da estrutura durante a corrida da aeronave na pista. Logo, supõe-se que, em 347,5s, o avião decola. Neste ponto, ocorre um leve aumento na altitude e na velocidade, o que pode ser relacionado com a eliminação do atrito entre o trem de pouso e o solo. Nesse momento, a velocidade indicada pelo instrumento é de 6m/s, aproximadamente. Apesar da faixa de trabalho do instrumento ser de 8 a 15,5m/s, destaca-se que devido à baixa carga carregada pela aeronave, analiticamente era esperado que a decolagem fosse ocorrer próximo a 6m/s.

Figura 7: Altitude em relação ao solo durante a decolagem.

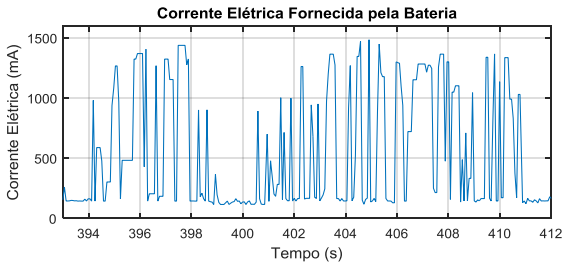
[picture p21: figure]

P á g i n a 7 | 8

### 6 FORUM SAE BRASIL AERODESIGN 2018

Através da Figura 7, verifica-se que o instrumento indica que a aeronave está a 2 metros abaixo do nível do solo no instante 347,5s. Neste ponto, o erro absoluto apresentado pelo instrumento ultrapassa, portanto, o limite de erro tolerado de 0,5m para este projeto. A partir deste instante, a altitude da aeronave sobe de maneira condizente com o voo. Contudo, a medição de altitude não está satisfatória quando comparada aos requisitos apresentados.

### 2. Rolamento e Arfagem

A Figura 8 e a Figura 9 apresentam os valores calculados para os ângulos de rolamento e arfagem, respectivamente, durante o procedimento de decolagem. Em 347,5s, destacado nos dois gráficos abaixo, ocorre a decolagem da aeronave.

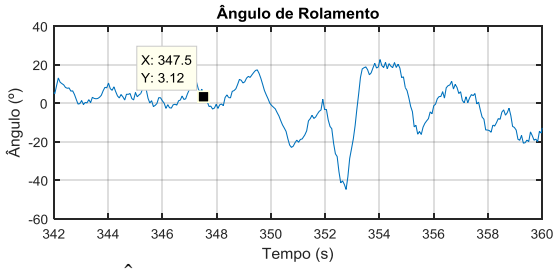
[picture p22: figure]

Figura 8: Ângulo de rolamento durante a decolagem.

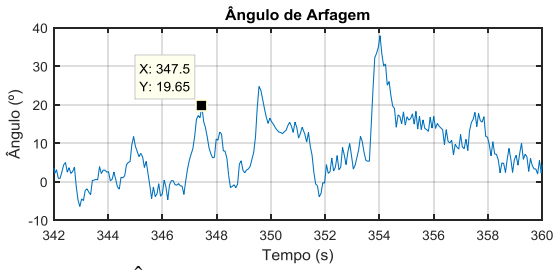
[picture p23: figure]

Figura 9: Ângulo de arfagem durante a decolagem.

Através da Figura 8, nota-se que a amplitude da resposta é maior a partir do ponto de decolagem, o que condiz com a aeronave em voo, devido às manobras e ação dos ventos, sem ser limitado pelo suporte do trem de pouso. Mesmo que a aeronave tenha sido projetada para uma rápida resposta de rolamento, este se tornou maior que o esperado, possivelmente devido à baixa carga utilizada no voo.

Na Figura 9, pode ser analisado o comportamento da aeronave em resposta aos comandos de profundor efetuados pelo piloto e a estabilização da arfagem; nota-se um aumento rápido e uma queda mais suave. Pode ser visto uma relação de 350s a 352s entre os gráficos, onde há uma leve queda na velocidade e um considerável aumento na altitude, sendo uma resposta esperada em uma manobra de arfagem para ganho de altitude.

Isto também pode ser notado a partir de 352s, onde a aeronave se mantém a um ângulo de arfagem positivo, ganhando altitude, mas em velocidade constante.

### 3. Corrente Elétrica

Com o sensor de corrente elétrica instalado na aeronave, foi possível medir a corrente fornecida pela bateria durante o voo; o gráfico é apresentado na Figura 10. Para fins de validação do projeto, os resultados obtidos pelo sensor foram satisfatórios. Com ele, foi possível determinar que a corrente elétrica máxima drenada pelo sistema foi de, aproximadamente, 1,5A.

Figura 10: Corrente fornecida pela bateria durante o voo.

## CONCLUSÕES ESPERADAS

A plataforma desenvolvida foi extremamente satisfatória em seu desempenho, não apresentando problema quanto à gravação ou à transmissão dos dados. A partir dos dados obtidos, é possível realizar uma análise qualitativa e quantitativa do comportamento da aeronave durante o voo. Contudo, notaram-se alguns cuidados que devem ser tomados para que as medições se tornem confiáveis.

Notou-se a forte influência da vibração do motor nos dados obtidos de velocidade e orientação da aeronave. A estrutura do avião (e, consequentemente, o tubo de Pitot, o sensor de pressão diferencial e o acelerômetro) está submetida à vibração mecânica na frequência de rotação do motor, que pode variar de 58 a 210Hz. Para uma análise dos sinais de frequências inferiores a 210Hz, propõe-se que um teste seja realizado de modo a coletar o sinal do sensor de pressão diferencial a uma frequência superior a 420Hz. Assim, ruídos poderão ser identificados e filtros poderão ser projetados de modo a atenuar a perturbação proveniente da vibração mecânica da estrutura. Para a realização do teste, a taxa de amostragem pode ser aumentada com a criação de um buffer de dados. Sugere-se que, a partir de um comando dado pelo usuário, o sistema realize um conjunto de amostragens por um tempo fixo, armazenando as informações em um buffer. Depois de transcorrido um determinado tempo, esses dados poderão ser gravados no cartão de memória.

P á g i n a 8 | 8

### 6 FORUM SAE BRASIL AERODESIGN 2018

Após a realização do teste de vibração, sugere-se que seja incluído um filtro analógico na resposta do sensor. Filtros digitais também podem ser utilizados; contudo, somente se a frequência de amostragem for duas vezes maior que a frequência de corte do filtro. O fabricante desse sensor indica que, mesmo com a utilização de filtros, seja realizada a média móvel dos sinais amostrados com, no mínimo, oito amostras, de modo a garantir atenuação de erros aleatórios.

De modo a tornar o dado de orientação da aeronave mais confiável e menos influenciado pela vibração da estrutura, propõe-se a utilização da biblioteca de código aberto de Rowberg (2017). Com ela, é possível coletar a orientação calculada pelo processador interno presente no MPU-6050.

Após a realização dos testes e implantação dos filtros, pode-se alterar a rotina da coleta de dados. Para cada sensor, propõe-se que um conjunto de medições seja realizado em cada iteração para o cálculo da média desse conjunto.

Em trabalhos futuros, pode-se também estudar a influência da temperatura no resultado do sensor de pressão diferencial MPX7002DP. O erro de medição máximo apresentado pelo fabricante inclui variações de temperatura de 5ºC. Tendo conhecimento da variação da resposta em função da diferença de temperatura, pode-se reduzir uma parcela do erro sistemático e aprimorar a resposta do sensor.

O posicionamento do tubo de Pitot na aeronave pode interferir na resposta do sensor, devido às influências aerodinâmicas causadas pela estrutura do avião. Sugere-se que, com o tubo de Pitot instalado em uma asa, seja realizado um novo ensaio com uma parcela da asa dentro de um túnel de vento. Assim, será possível comparar a resposta do sensor com e sem a influência aerodinâmica da asa.

Para a determinação do erro das medições de orientação e de altitude, propõe-se a utilização de uma placa controladora comercial de voo para a tomada de medidas de referência. Com esses dados, é possível então comparar os resultados e determinar o erro máximo atingido pela plataforma desenvolvida.

## REFERÊNCIAS

ADAFRUIT. Repositório da Biblioteca Adafruit_INA219. GitHub, 2017. Disponivel em: <https://github.com/adafruit/Adafruit_INA219>. Acesso em: 10 out. 2017.

ARDUPILOT. Repositório da Biblioteca SiK. GitHub, 2017. Disponivel em: <https://github.com/ArduPilot/SiK>. Acesso em: 25 nov. 2017.

BALBINOT, A.; BRUSAMARELLO, V. J. Instrumentação e Fundamentos de Medidas. 2. ed. Rio de Janeiro: LTC, v. 1, 2011.

GREIMAN, B. Repositório da Biblioteca SdFat. GitHub, 2017. Disponivel em: <https://github.com/greiman/SdFat>. Acesso em: 2 out. 2017.

KUNDU, A. K. Aircraft Design. New York City: Cambridge University Press, 2010.

LAN, C. E.; ROSKAM, J. Airplane Aerodynamics and Performace. Lawrence: DARcorporation, 2003.

OJHA, S. Flight Performance of Aircraft. Bombay: American Institute of Aeronautics and Astronautics.

PAVLOCK, K. M. Flight Test Engineering. Edwards: Purdue University, 2013.

ROWBERG, J. Repositório da Biblioteca MPU6050. GitHub, 2017. Disponivel em:
<https://github.com/jrowberg/i2cdevlib/tree/master/Arduino/MPU6050>. Acesso em: 25 ago. 2017.

SAE BRASIL AeroDesign. Regras e Relatórios, 2017. Disponivel em: <http://portal.saebrasil.org.br/programas-estudantis/sae-brasil-aerodesign/regras>. Acesso em: 1 set. 2017.

SMINGHUB. Repositório da Biblioteca BMP180. GitHub, 2017. Disponivel em:
<https://github.com/SmingHub/SmingRTOS/tree/master/sming/libraries/BMP180>. Acesso em: 10 maio 2017.

## CONTATO

Túlio Dapper e Silva
Universidade Federal do Rio Grande do Sul tuliodapper@gmail.com

Vinicius Cabreira
Universidade Federal do Rio Grande do Sul vinicius.cabreira@outlook.com

Edison Pignaton de Freitas
Universidade Federal do Rio Grande do Sul edison.pignaton@ufrgs.br

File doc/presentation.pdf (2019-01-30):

## Instrumentação de um veículo aéreo não tripulado para validação de seu projeto

Autor: Túlio Dapper e Silva Orientador: Edison Pignaton de Freitas

UNIVERSIDADE FEDERAL DO RIO GRANDE DO SUL

ESCOLA DE ENGENHARIA

TRABALHO DE CONCLUSÃO EM ENGENHARIA DE CONTROLE E AUTOMAÇÃO

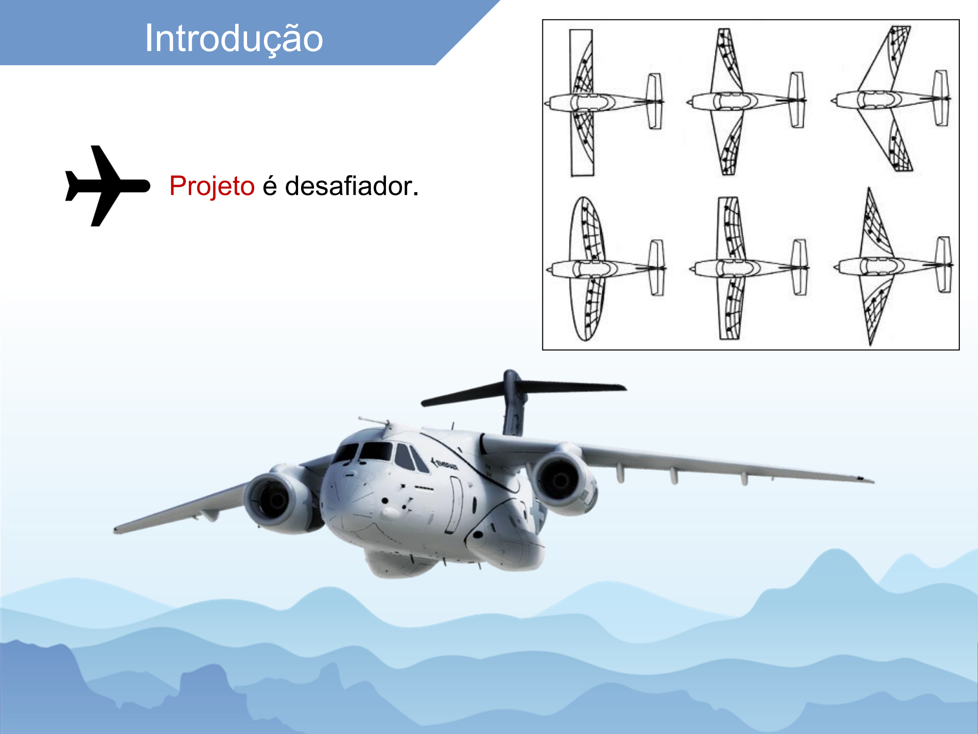
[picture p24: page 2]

Introdução

Projeto é desafiador.


Introdução

Projeto é desafiador.

Testes em voo são
essenciais.

KC-390:
1200 horas.
(G1, 2017)

- Sensoriamento de VANT para competição SAE BRASIL AeroDesign
- Velocidade em relação ao ar
- Orientação
- Altitude
- Corrente drenada pelo sistema elétrico

Objetivo

PERFORMANCE
DE VOO

Sumário

- Revisão Bibliográfica
- Requisitos do Projeto
- Desenvolvimento
- Componentes
- Placa de Aquisição de Dados
- Interfaces com o Usuário
- Apresentação e Discussão dos Resultados
- Conclusões
- Trabalhos Futuros

Sumário

- Revisão Bibliográfica
- Requisitos do Projeto
- Desenvolvimento
- Componentes
- Placa de Aquisição de Dados
- Interfaces com o Usuário
- Apresentação e Discussão dos Resultados
- Conclusões
- Trabalhos Futuros

Revisão Bibliográfica | Velocidade

Pressão de Estagnação

(Hall, 2017)

(Schneider, 2000)

Escoamentos incompressíveis:

Pressão
Estática

- Representação
- Ângulos de Euler, Quaterniões e Matriz Rotacional
- Ângulos de Euler


- Quais sensores podem ser utilizados?
Revisão Bibliográfica | Orientação

(Leccadito, 2013)


(Leccadito, 2013) | (Elettronica Open Source, 2011)
Revisão Bibliográfica | Orientação
↓ Forças externas | ↓ Integração discreta
Acelerômetro | Giroscópio

Revisão Bibliográfica | Orientação
- Fusão de Dados
- Combinação das vantagens de cada sensor
- Filtro de Kalman e Filtro Complementar
- Filtro Complementar
- Acelerômetro:
- Atenuar as vibrações
- Giroscópio
- Eliminar o erro acumulado
Ganho | Combinação

Sumário

- Revisão Bibliográfica
- Requisitos do Projeto
- Desenvolvimento
- Componentes
- Placa de Aquisição de Dados
- Interfaces com o Usuário
- Apresentação e Discussão dos Resultados
- Conclusões
- Trabalhos Futuros

- Erro máximo admissível: 50mA.
- Período de amostragem
máximo: 70ms.
- Erro máximo admissível: 1º.
- Mínimo: 10m/s.
- Máximo: 20m/s.
- Erro máximo admissível:
0,5m/s.
Velocidade em Relação ao Ar | Orientação
Altitude | Corrente Elétrica

Requisitos do Projeto

- Erro máximo admissível: 0,5m.

Sumário

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

Desenvolvimento | Componentes
Processamento | Orientação e Altitude

Corrente Elétrica

Gravação dos dados
em cartão SD | Telemetria

Velocidade do Ar

Desenvolvimento | Componentes
Processamento | Orientação e Altitude

Corrente Elétrica

Gravação dos dados
em cartão SD | Telemetria

Velocidade do Ar

Desenvolvimento | Componentes
Processamento | Orientação e Altitude

Corrente Elétrica

Gravação dos dados
em cartão SD | Telemetria

Velocidade do Ar

Desenvolvimento | Componentes
Processamento | Orientação e Altitude

Corrente Elétrica

Gravação dos dados
em cartão SD | Telemetria

Velocidade do Ar

Desenvolvimento | Componentes

Sensor de Pressão Diferencial

- Falta de interesse: 0 a 250Pa
- MPX7002DP
- -2kPa a 2kPa
- Analógico
- Baixo custo
- MS4525DO-DS3BK002DPL
- 0 a 500Pa
- Digital: Comunicação I2C

Desenvolvimento; Componentes; ▪ Por que insistir?

Sensor de Pressão Diferencial: MPX7002DP

Desenvolvimento; Componentes; ▪ Precisamos validar...

Sensor de Pressão Diferencial: MPX7002DP

Desenvolvimento; Componentes

Sensor de Pressão Diferencial: MPX7002DP

✓ Faixa de trabalho: 8 a 15,5m/s.

Desenvolvimento | Componentes
Processamento | Orientação e Altitude

Corrente Elétrica

Gravação dos dados
em cartão SD | Telemetria

Velocidade do Ar

Desenvolvimento | Componentes
Processamento | Orientação e Altitude

Corrente Elétrica

Gravação dos dados
em cartão SD | Telemetria

Velocidade do Ar

Desenvolvimento | Componentes

Acelerômetro, Giroscópio, Barômetro e Termômetro

- GY-87
- Digital: Comunicação I2C
- MPU6050: Acelerômetro e Giroscópio
- BMP180: Barômetro e Termômetro
- GY-80
- GY-91

Desenvolvimento | Componentes
Processamento | Orientação e Altitude

Corrente Elétrica

Gravação dos dados

em cartão SD | Telemetria

Velocidade do Ar

Desenvolvimento | Componentes
Processamento | Orientação e Altitude

Corrente Elétrica

Gravação dos dados

em cartão SD | Telemetria

Velocidade do Ar

Desenvolvimento | Componentes

Sensor de Corrente Elétrica

✓ INA219 + R100
- Resistor shunt
- -3,2A a 3,2A
- Digital: Comunicação I2C
- Calibrado
- ACS712
- Efeito Hall
- -5A a 5A
- Analógico
- Baixo custo

Desenvolvimento | Componentes
Processamento | Orientação e Altitude

Corrente Elétrica

Gravação dos dados


em cartão SD | Telemetria

Velocidade do Ar

Desenvolvimento | Componentes
Processamento | Orientação e Altitude

Corrente Elétrica

Gravação dos dados

em cartão SD | Telemetria

Velocidade do Ar

Desenvolvimento | Componentes
Processamento | Orientação e Altitude

Corrente Elétrica

Gravação dos dados
em cartão SD | Telemetria

Velocidade do Ar

Desenvolvimento | Componentes
Processamento | Orientação e Altitude

Corrente Elétrica

Gravação dos dados
em cartão SD | Telemetria

Velocidade do Ar

Desenvolvimento | Componentes

Telemetria

✓3DR
- Firmware de código aberto: SiK
- 433MHz ou 915MHz
- Baixo custo
- XBee
- Protocolo de comunicação: ZigBee
- Frequência ISM

Desenvolvimento | Componentes
Processamento | Orientação e Altitude

Corrente Elétrica

Gravação dos dados

em cartão SD | Telemetria

Velocidade do Ar


Regulador de Tensão

Desenvolvimento | Placa de Aquisição

Firmware

- Gravação dos dados em arquivos partilhados
- Cálculo da orientação | +
| Gravação em novo arquivo | = | 33ms
- 1ª Iteração: aquisição dos dados
- 2ª Iteração: gravação e envio dos dados por telemetria
- | Período de gravação | = | 66ms
Desenvolvimento | Placa de Aquisição

Desenvolvimento | Interface

Telemetria


Desenvolvimento | Interface

Análise dos Dados


Desenvolvimento | Instalação

Sumário

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


Resultados

Resultados Resultados | Velocidade

Decolagem


- Média móvel de 3 valores. | 41

Resultados Resultados | Velocidade

Decolagem


- Média móvel de 3 valores. | 42

Resultados Resultados | Velocidade

Manobra de descida


- Média móvel de 3 valores. | 43

Resultados Resultados | Velocidade

Manobra de descida


- Média móvel de 3 valores. | 44

Resultados Resultados | Velocidade

↑ Avaliação do comportamento da aeronave.

↓ Caráter oscilatório.

↓ Faixa de trabalho de 8 a 15,5m/s.

↓ Diferença das condições de medição
- Calibração: 100 amostras em intervalos de 50ms.
- Teste: 3 amostras em intervalos de 66ms.
- Não está satisfatório.

Resultados Resultados | Altitude


- Média móvel de 3 valores.
↓ Ultrapassa o erro máximo tolerado.
- Não está satisfatório.

Decolagem

Resultados Resultados; Rolamento e Arfagem; Decolagem

↓ Caráter oscilatório.
▪ Não está satisfatório.

Resultados Resultados; Rolamento e Arfagem; Decolagem

▪ Média móvel de 3 valores.
↑ Avaliação do comportamento da aeronave.

Corrente Elétrica Resultados Resultados; Corrente Elétrica; ▪ Satisfatório.

↑ Plataforma de aquisição e transmissão dados estão satisfatórios.

↑ É possível avaliar características da aeronave com os resultados obtidos.

↓ Resultados de velocidade do ar e orientação não estão satisfatórios devido, basicamente, à vibração mecânica da estrutura.

Conclusões

Trabalhos Futuros

- Identificar a influência da vibração mecânica na resposta de velocidade do ar e aceleração realizando a coleta dos dados a uma frequência superior a 420Hz.
- Estudar a influência da temperatura no resultado no sensor de pressão diferencial MPX7002DP.
- Comparar a resposta do sensor com e sem a influência aerodinâmica da asa em um túnel de vento.
- Comparar os resultados de orientação e altitude com instrumentos comerciais.

Referências

G1. Avião militar da Embraer tem incidente durante voo de teste em Gavião Peixoto, SP. G1, 2017. Disponível em: <https://g1.globo.com/sp/sao-carlos-regiao/noticia/aviao-militar-da-embraer-tem-incidente-durante-voo-de-teste-em-gaviao-peixoto-sp.ghtml>. Acesso em: 15 dez. 2017.

ELETTRONICA OPEN SOURCE. Sensori MEMS offrono dieci gradi di libertà. Elettronica Open Source, 2011. Disponível em: <https://it.emcelettronica.com/sensori-mems-offrono-dieci-gradi-di-liberta>. Acesso em: 14 dez. 2017.

HALL, N. Pitot-Static Tube. NASA, 2015. Disponível em: < https://www.grc.nasa.gov/www/k-12/airplane/pitot.html>. Acesso em: 14 dez. 2017.

SCHNEIDER, P. S. Medição de Velocidade e Vazão de Fluidos. Porto Alegre: Universidade Federal do Rio Grande do Sul, 2000. Apostila para disciplina "Medições Térmicas".

LECCADITO, M. A Kalman Filter Based Atitude Heading Reference System Using a Low Cost Inertial Measurement Unit. Richmond. 2013.
Dissertação de Mestrado em Ciência. | 52

Fim

# OBRIGADO!

☺ ☺ ☺


Extra Resultados | Animação

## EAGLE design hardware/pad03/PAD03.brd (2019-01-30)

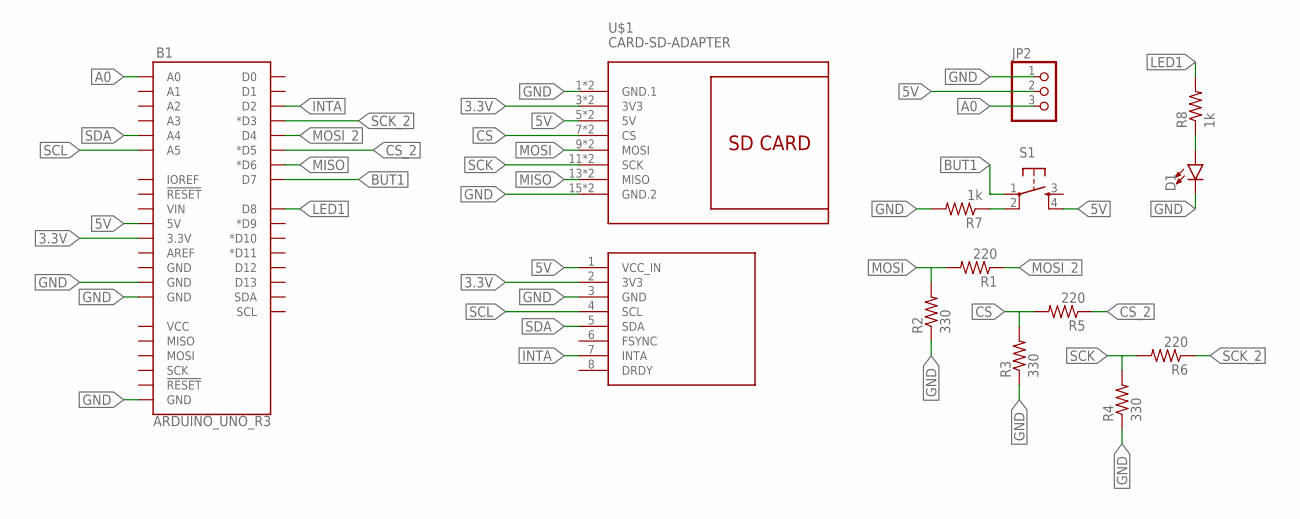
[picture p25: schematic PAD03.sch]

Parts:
B1: ARDUINO_UNO_R3; ARDUINO_R3
D1: LED5MM; LED_5MM
JP2: PINHD-1X3; 1X03
R1, R5, R6: 220; 0204/7
R2, R3, R4: 330; 0204/7
R7, R8: 1k; 0204/7
S1: TAC_SWITCHPTH; TACTILE-PTH
U$1: CARD-SD-ADAPTER
U$2: GY-86

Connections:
3.3V: B1.3.3V, U$1.3 (3V3), U$1.4 (3V3), U$2.2 (3V3)
5V: B1.5V, JP2.2, S1.4, U$1.5 (5V), U$1.6 (5V), U$2.1 (VCC_IN)
A0: B1.A0, JP2.3
BUT1: B1.D7, S1.1
CS: R3.2, R5.2, U$1.7 (CS), U$1.8 (CS)
CS_2: B1.D5 (*D5), R5.1
GND: B1.GND@1 (GND), B1.GND@2 (GND), B1.GND@3 (GND), D1.K (C), JP2.1, R2.1, R3.1, R4.1, R7.2, U$1.1 (GND.1), U$1.2 (GND.1), U$1.15 (GND.2), U$1.16 (GND.2), U$2.3 (GND)
INTA: B1.D2, U$2.7 (INTA)
LED1: B1.D8, R8.2
MISO: B1.D6 (*D6), U$1.13 (MISO), U$1.14 (MISO)
MOSI: R1.2, R2.2, U$1.9 (MOSI), U$1.10 (MOSI)
MOSI_2: B1.D4, R1.1
unnamed: R7.1, S1.2
unnamed: D1.A, R8.1
SCK: R4.2, R6.2, U$1.11 (SCK), U$1.12 (SCK)
SCK_2: B1.D3 (*D3), R6.1
SCL: B1.A5, U$2.4 (SCL)
SDA: B1.A4, U$2.5 (SDA)

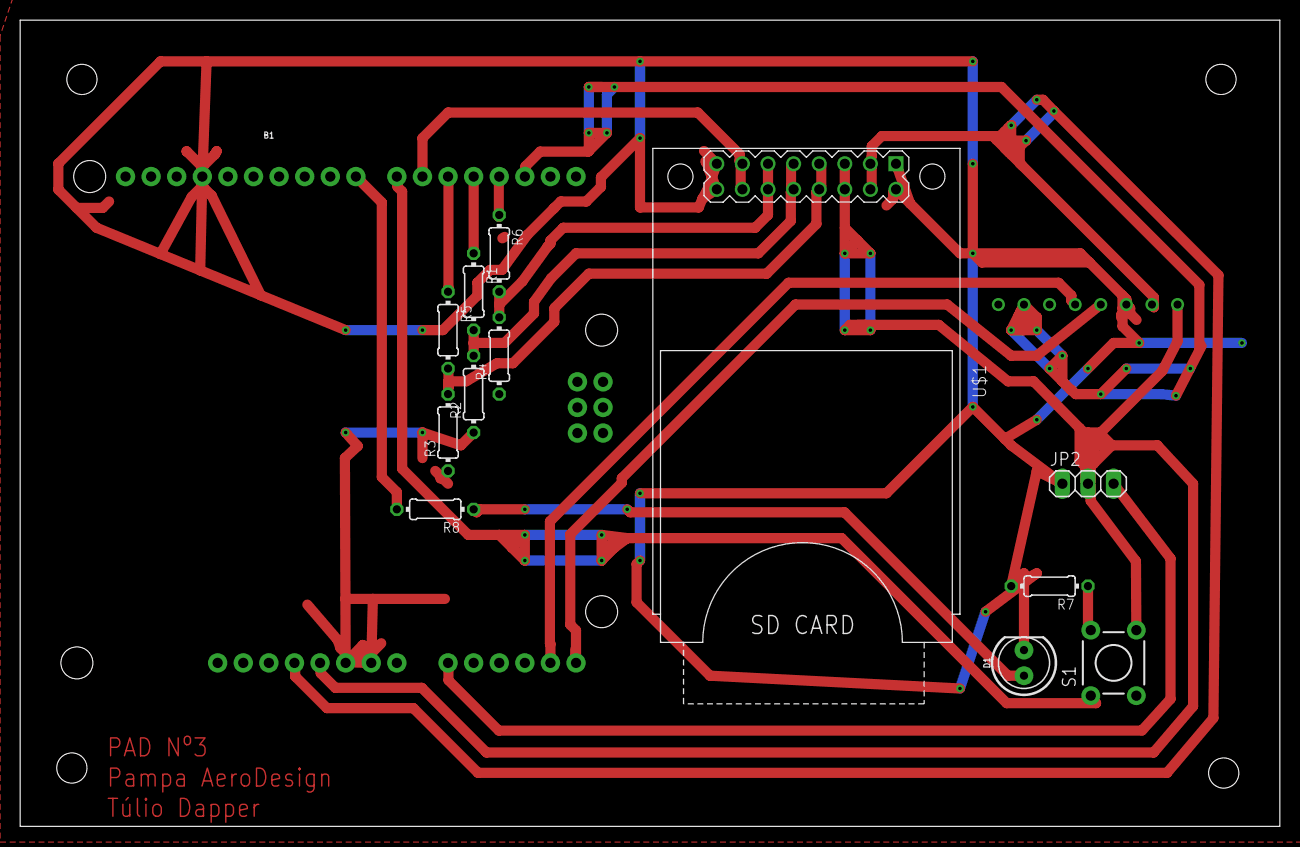
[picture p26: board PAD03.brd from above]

Board: 2 copper layers, 125.0 x 80.0 mm, 14 parts (1 on the bottom side), 18 nets.

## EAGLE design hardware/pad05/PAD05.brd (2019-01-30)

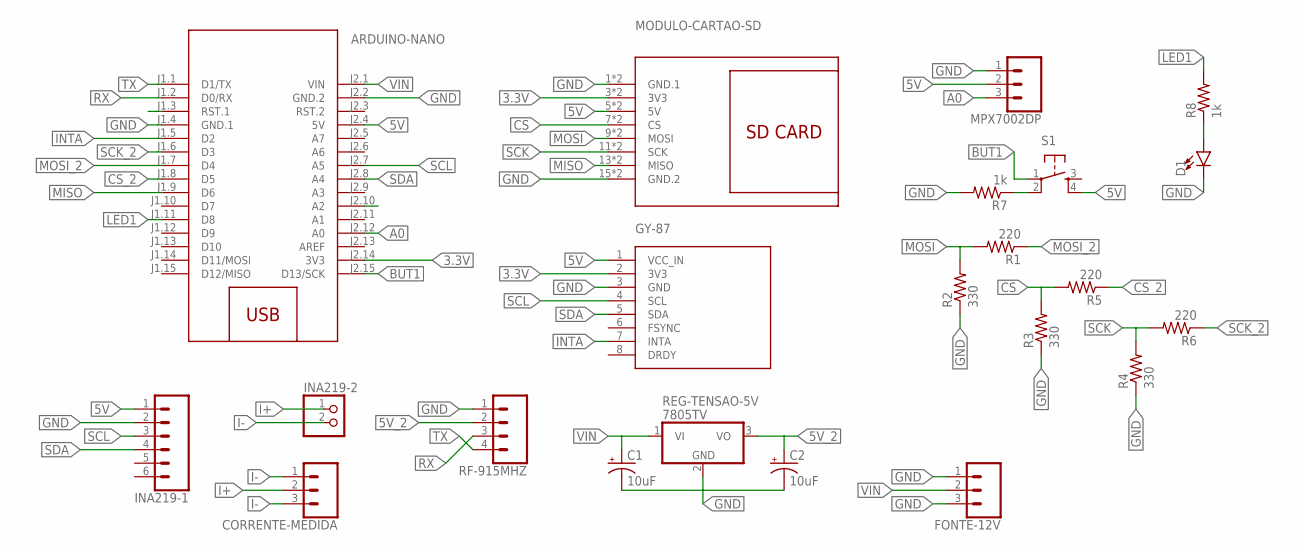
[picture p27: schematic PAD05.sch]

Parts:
ARDUINO-NANO: ARDUINO-NANO-3.0
C1, C2: 10uF; CPOL-RADIAL-2.5MM-5MM
CORRENTE-MEDIDA: CONN_03POLAR; MOLEX-1X3
D1: LED5MM; LED_5MM
FONTE-12V: CONN_03POLAR; MOLEX-1X3
GY-87: GY-86
INA219-1: CONN_06SILK_FEMALE_PTH; 1X06
INA219-2: PINHD-1X2; 1X02
MODULO-CARTAO-SD: CARD-SD-ADAPTER
MPX7002DP: CONN_03POLAR; MOLEX-1X3
R1, R5, R6: 220; 0204/7
R2, R3, R4: 330; 0204/7
R7, R8: 1k; 0204/7
REG-TENSAO-5V: 7805TV; TO220V
RF-915MHZ: CONN_04; 1X04
S1: TAC_SWITCHPTH; TACTILE-PTH

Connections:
3.3V: ARDUINO-NANO.J2.14 (3V3), GY-87.2 (3V3), MODULO-CARTAO-SD.3 (3V3), MODULO-CARTAO-SD.4 (3V3)
5V: ARDUINO-NANO.J1.3 (RST.1), ARDUINO-NANO.J2.4 (5V), GY-87.1 (VCC_IN), INA219-1.1, MODULO-CARTAO-SD.5 (5V), MODULO-CARTAO-SD.6 (5V), MPX7002DP.2, S1.4
5V_2: C2.1 (+), REG-TENSAO-5V.3 (VO), RF-915MHZ.2
A0: ARDUINO-NANO.J2.12 (A0), MPX7002DP.3
BUT1: ARDUINO-NANO.J2.15 (D13/SCK), S1.1
CS: MODULO-CARTAO-SD.7 (CS), MODULO-CARTAO-SD.8 (CS), R3.2, R5.2
CS_2: ARDUINO-NANO.J1.8 (D5), R5.1
GND: ARDUINO-NANO.J1.4 (GND.1), ARDUINO-NANO.J2.2 (GND.2), C1.2 (-), C2.2 (-), D1.K (C), FONTE-12V.1, FONTE-12V.3, GY-87.3 (GND), INA219-1.2, MODULO-CARTAO-SD.1 (GND.1), MODULO-CARTAO-SD.2 (GND.1), MODULO-CARTAO-SD.15 (GND.2), MODULO-CARTAO-SD.16 (GND.2), MPX7002DP.1, R2.1, R3.1, R4.1, R7.2, REG-TENSAO-5V.2 (GND), RF-915MHZ.1
I+: CORRENTE-MEDIDA.2, INA219-2.1
I-: CORRENTE-MEDIDA.1, CORRENTE-MEDIDA.3, INA219-2.2
INTA: ARDUINO-NANO.J1.5 (D2), ARDUINO-NANO.J2.10 (A2), GY-87.7 (INTA)
LED1: ARDUINO-NANO.J1.11 (D8), R8.2
MISO: ARDUINO-NANO.J1.9 (D6), MODULO-CARTAO-SD.13 (MISO), MODULO-CARTAO-SD.14 (MISO)
MOSI: MODULO-CARTAO-SD.9 (MOSI), MODULO-CARTAO-SD.10 (MOSI), R1.2, R2.2
MOSI_2: ARDUINO-NANO.J1.7 (D4), R1.1
unnamed: R7.1, S1.2
unnamed: D1.A, R8.1
RX: ARDUINO-NANO.J1.2 (D0/RX), RF-915MHZ.3
SCK: MODULO-CARTAO-SD.11 (SCK), MODULO-CARTAO-SD.12 (SCK), R4.2, R6.2
SCK_2: ARDUINO-NANO.J1.6 (D3), R6.1
SCL: ARDUINO-NANO.J2.7 (A5), GY-87.4 (SCL), INA219-1.3
SDA: ARDUINO-NANO.J2.8 (A4), GY-87.5 (SDA), INA219-1.4
TX: ARDUINO-NANO.J1.1 (D1/TX), RF-915MHZ.4
VIN: ARDUINO-NANO.J2.1 (VIN), C1.1 (+), FONTE-12V.2, REG-TENSAO-5V.1 (VI)

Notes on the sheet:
GY-87

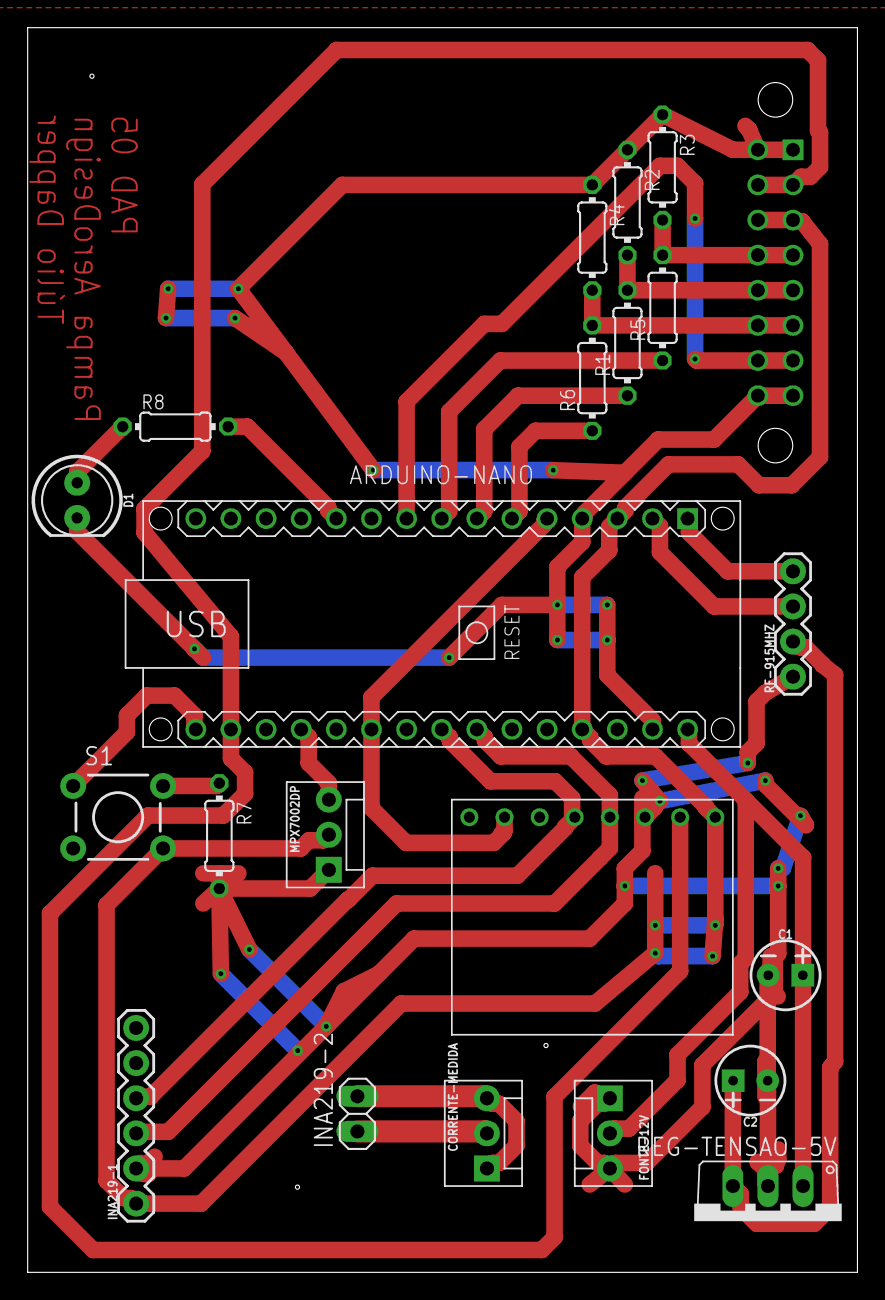
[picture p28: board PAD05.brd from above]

Board: 2 copper layers, 60.0 x 90.0 mm, 22 parts (1 on the bottom side), 24 nets.

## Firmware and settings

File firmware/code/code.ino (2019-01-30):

#include <Wire.h>
#include "I2Cdev.h"
#include "MPU6050_6Axis_MotionApps20.h"
#include <BMP180.h>
#include <Adafruit_INA219.h>
#include <SdFat.h> // Cartao SD

#define DELAY_MS 200

// ### CARTAO SD ####
SdFat sdCard;
SdFile meuArquivo;
const int chipSelect = 5; // Pino ligado ao CS do modulo

// ### ACELEROMETRO ####
#define PINO_INTERRUPCAO 2  // use pin 2 on Arduino Uno & most boards
MPU6050 mpu;
Quaternion q;           // [w, x, y, z]         quaternion container
VectorInt16 aa;         // [x, y, z]            accel sensor measurements
VectorFloat gravity;    // [x, y, z]            gravity vector
VectorInt16 aaReal;     // [x, y, z]            gravity-free accel sensor measurements
uint8_t mpuIntStatus;   // holds actual interrupt status byte from MPU
uint8_t devStatus;      // return status after each device operation (0 = success, !0 = error)
uint16_t packetSize;    // expected DMP packet size (default is 42 bytes)
uint16_t fifoCount;     // count of all bytes currently in FIFO
uint8_t fifoBuffer[64]; // FIFO storage buffer
volatile bool mpuInterrupt = false;     // indicates whether MPU interrupt pin has gone high

// ### SENSOR PRESSAO DIFERENCIAL ####
#define A 0.0378
#define B 0.0378
#define C -0.9244
#define NUM_AMOSTRAS_PRESSAO_DIFERENCIAL 125
#define PINO_PRESSAO_DIFERENCIAL A0
double ValorPrDif = 0;

// ### MEDIDOR DE CORRENTE ####
Adafruit_INA219 ina219;
int ValorMedCorr = 0;  

// ### BAROMETRO ###
BMP180 barometer;
long ValorPressao = 0;
double ValorTemperatura = 0;

// ### BOTAO ####
#define PIN0_BOTAO_INICIAR_PAUSAR 13
#define debounceDelay 50
int btn_begin;             
int btn_begin_last = LOW;
unsigned long lastDebounceTime_btn_begin = 0;

// ### LED ####
#define PINO_LED 8
int sgn_led = LOW;

// ### VARIÁVEIS GERAIS ####
int b_transmitindo = 0;
int b_gravando     = 0;

int b_ler_sensor_pressao_diferencial = 0;
int b_ler_orientacao         = 0;
int b_ler_pressao            = 0;
int b_ler_corrente_eletrica  = 0;
int b_ler_velocidade_roda    = 0;
int b_ler_aceleracao         = 0;

int b_habilitado_cartao_sd         = 0;
int b_habilitado_orientacao_aceleracao = 0;
int b_habilitado_pressao           = 0;
int b_habilitado_velocidade_roda   = 0;

unsigned long tempo_inicio = 0;
unsigned long tempo_fim = 0;

// ### FUNÇÕES ####
void gravar_dados();
void enviar_dados();
void ler_sensor_pressao_diferencial();
void ler_orientacao_aceleracao();
void ler_pressao();
void ler_corrente_eletrica();
void ler_velocidade_roda();

void dmpDataReady();
int iniciar_arquivo();
void sinalizar(int tempo);
void aguarda(unsigned long tempo_max);

void setup() {
  
  // Define as entradas
  pinMode(PINO_PRESSAO_DIFERENCIAL, INPUT);
  pinMode(PIN0_BOTAO_INICIAR_PAUSAR, INPUT);
  pinMode(PINO_INTERRUPCAO, INPUT);
    
  // Define as saidas
  pinMode(PINO_LED, OUTPUT);
   
  // ## SERIAL ## Obs: Tranca se não tiver comunicação serial funcionando, pois telemetria é fundamental para o funcionamento do sistema.
  Serial.begin(57600);   
  if (!Serial) {
    while(1) { sinalizar(100); }
  }
  
  // ## CARTÃO SD ##
  if(sdCard.begin(chipSelect,SPI_HALF_SPEED)){
    b_habilitado_cartao_sd = 1;
  }
  
  // ### ACELEROMETRO ####  
  Wire.begin();
  Wire.setClock(400000); // 400kHz I2C clock. Comment this line if having compilation difficulties
  mpu.initialize();
  devStatus = mpu.dmpInitialize();
  mpu.setDLPFMode(MPU6050_DLPF_BW_5);
  mpu.setXGyroOffset(68);
  mpu.setYGyroOffset(-8);
  mpu.setZGyroOffset(-20);
  mpu.setXAccelOffset(963);
  mpu.setYAccelOffset(-3524);
  mpu.setZAccelOffset(720);
  if (devStatus == 0) {
    b_habilitado_orientacao_aceleracao = 1;
  }

  // ### BAROMETRO ####  
  barometer = BMP180();
  if(barometer.EnsureConnected())
  {
    barometer.SoftReset();
    barometer.Initialize();
    b_habilitado_pressao  = 1;
  }
  
  // ### MEDIDOR DE CORRENTE ### Obs: o sensor de corrente não tem verificação se está habilitado ou não.
  ina219.begin();
  
}

// ================================================================
// ===                    MAIN PROGRAM LOOP                     ===
// ================================================================

void loop() {

  char data[30];
  char nome_arquivo[15];
  char numero;
  char i;
  char caracter;

  // Se não está gravando em cartão SD e não está transmitindo por telemetria, então aguarda comando de gravação e/ou transmissão.
  while ((b_gravando == 0) && (b_transmitindo == 0)){
    if(Serial.available()){
      numero = Serial.readBytesUntil('|',data,30);
      data[numero] = 0;
      // Protocolo de inicio de coleta de dados : "b_transmitindo;b_gravando;b_ler_sensor_pressao_diferencial;b_ler_orientacao;b_ler_pressao;b_ler_corrente_eletrica;b_ler_velocidade_roda;b_ler_aceleracao;nome_arquivo"
      i = sscanf((char*)data,"%d;%d;%d;%d;%d;%d;%d;%d;%s", &b_transmitindo, &b_gravando, &b_ler_sensor_pressao_diferencial, &b_ler_orientacao, &b_ler_pressao, &b_ler_corrente_eletrica, &b_ler_velocidade_roda, &b_ler_aceleracao, nome_arquivo);
      // Confere integridade da mensagem de inicio de coleta de dados
      if (i == 9){
        // Cria arquivo com o nome se b_gravando = 1
        if (b_gravando == 1) {
          if (!meuArquivo.open(nome_arquivo, O_WRITE | O_CREAT | O_AT_END)) {
            b_gravando = 0;
          }
        }
        // Inicializa a interrupção do MPU-6050 se (b_ler_orientacao == 1) || (b_ler_aceleracao == 1)
        if ((b_ler_orientacao == 1) || (b_ler_aceleracao == 1)) {
          mpu.setDMPEnabled(true);
          attachInterrupt(digitalPinToInterrupt(PINO_INTERRUPCAO), dmpDataReady, RISING);
          mpuIntStatus = mpu.getIntStatus();
          packetSize = mpu.dmpGetFIFOPacketSize();
          mpu.resetFIFO();
        }
        tempo_inicio = millis();
        
      // Se a mensagem não se encaixou em uma mensagem de inicio de coleta de dados, então pode ser que...
      } else {
        b_transmitindo  = 0;
        b_gravando      = 0;
        
        i = sscanf((char*)data, "%s", nome_arquivo);
        if (i == 1){
          // Confere se é um comando de Pausar; se sim, manda ok, pq está parado mesmo...
          if (nome_arquivo[0] == 'p'){
            Serial.println("o");
          // Confere se é um comando de Enviar Habilitados; se sim, envia...
          } else if (nome_arquivo[0] == 'i'){
            enviar_habilitados();
          }
        }
      }
    }
    
    if (b_gravando == 1) {
      // Inserir Colunas
      meuArquivo.println("Tempo;PrDif;Q.w;Q.x;Q.y;Q.z;Pressao;Corrente;VelRoda;Acel.x;Acel.y;Acel.z");
      // Inserir Medidas Habilitadas
      meuArquivo.print("1;");
      meuArquivo.print(b_ler_sensor_pressao_diferencial);
      meuArquivo.print(';');
      meuArquivo.print(b_ler_orientacao);
      meuArquivo.print(';');
      meuArquivo.print(b_ler_orientacao);
      meuArquivo.print(';');
      meuArquivo.print(b_ler_orientacao);
      meuArquivo.print(';');
      meuArquivo.print(b_ler_orientacao);
      meuArquivo.print(';');
      meuArquivo.print(b_ler_pressao);
      meuArquivo.print(';');
      meuArquivo.print(b_ler_corrente_eletrica);
      meuArquivo.print(';');
      meuArquivo.print(b_ler_velocidade_roda);
      meuArquivo.print(';');
      meuArquivo.print(b_ler_aceleracao);
      meuArquivo.print(';');
      meuArquivo.print(b_ler_aceleracao);
      meuArquivo.print(';');
      meuArquivo.println(b_ler_aceleracao);
    }
    
    if ((b_gravando == 1) || (b_transmitindo == 1)){
      digitalWrite(PINO_LED, LOW);
      Serial.println("o");
    }
  }
  
  tempo_fim = millis();

  // Aguardar completar 50 ms
  if ((b_ler_orientacao == 1) || (b_ler_aceleracao == 1)) {
    while (!mpuInterrupt && fifoCount < packetSize){}
  } else {
    delay(DELAY_MS - (tempo_fim - tempo_inicio));
  }

  tempo_inicio = millis();

  if (b_ler_sensor_pressao_diferencial == 1) {
    ler_sensor_pressao_diferencial();
  }

  if ((b_ler_orientacao == 1) || (b_ler_aceleracao == 1)) {
    ler_orientacao_aceleracao();
  }

  if (b_ler_pressao == 1) {
    ler_pressao();
  }

  if (b_ler_corrente_eletrica == 1) {
    ler_corrente_eletrica();
  }

  if (b_ler_velocidade_roda == 1){
    ler_velocidade_roda();
  }

  if (b_gravando == 1) {
    gravar_dados();
  }

  if (b_transmitindo == 1){
    enviar_dados();
  }

  // Verifica se deve Pausar (comando "p")
  if(Serial.available()){
    numero = Serial.read();
    if (numero == 'p'){
        // Desabilita interrupção se estiver (b_ler_orientacao == 1) || (b_ler_aceleracao == 1)
        if ((b_ler_orientacao == 1) || (b_ler_aceleracao == 1)) {
          mpu.setDMPEnabled(false);
          detachInterrupt(digitalPinToInterrupt(PINO_INTERRUPCAO));
          mpuInterrupt = false;
        }
        // Fecha arquivo se estiver gravando
        if (b_gravando == 1) {
          meuArquivo.close();
          b_gravando = 0;
        }
        b_transmitindo = 0;
        // Envia Ok
        Serial.println("o");
    }
  }

}

void ler_sensor_pressao_diferencial(){
  uint16_t velocidade_amostrada_anterior = 0;
  char i;
  ValorPrDif = 0;
  for (i=0;i<NUM_AMOSTRAS_PRESSAO_DIFERENCIAL;i++){
    ValorPrDif = C*ValorPrDif + (double) (A*analogRead(PINO_PRESSAO_DIFERENCIAL)) + (double) (B*velocidade_amostrada_anterior);
    delayMicroseconds(1190);
  }
}

void ler_orientacao_aceleracao(){
  mpuInterrupt = false;
  mpuIntStatus = mpu.getIntStatus();
  fifoCount = mpu.getFIFOCount();
  if ((mpuIntStatus & 0x10) || fifoCount == 1024) {
      mpu.resetFIFO();
      digitalWrite(PINO_LED, HIGH);
  } else if (mpuIntStatus & 0x02) {
      while (fifoCount < packetSize) fifoCount = mpu.getFIFOCount();
      mpu.getFIFOBytes(fifoBuffer, packetSize);
      fifoCount -= packetSize;
      if ((b_ler_orientacao == 1) || (b_ler_aceleracao == 1)) {
        mpu.dmpGetQuaternion(&q, fifoBuffer); // q.w, q.x, q.y, q.z
      }
      if (b_ler_aceleracao == 1) {
        mpu.dmpGetAccel(&aa, fifoBuffer);
        mpu.dmpGetGravity(&gravity, &q);
        mpu.dmpGetLinearAccel(&aaReal, &aa, &gravity);
      }
  }
}

void ler_pressao(){
  if(barometer.IsConnected){
    ValorPressao = barometer.GetPressure();
  }
}

void ler_corrente_eletrica(){
  ValorMedCorr = ina219.getCurrent_mA();
}

void ler_velocidade_roda(){
  
}

void aguarda(unsigned long tempo_max){
}

void dmpDataReady() {
  mpuInterrupt = true;
}

void sinalizar(int tempo){
  digitalWrite(PINO_LED, HIGH);
  delay(100);
  digitalWrite(PINO_LED, LOW);
  delay(tempo);
  digitalWrite(PINO_LED, HIGH);
  delay(100);
  digitalWrite(PINO_LED, LOW);
  delay(tempo);
  digitalWrite(PINO_LED, HIGH); 
  delay(100);
  digitalWrite(PINO_LED, LOW);
  delay(tempo);
}

void gravar_dados(){
  // Tempo
  meuArquivo.print(tempo_inicio);
  meuArquivo.print(';');
  // Pressao Diferencial
  meuArquivo.print(ValorPrDif);
  meuArquivo.print(';');
  // Orientação
  meuArquivo.print(q.w);
  meuArquivo.print(';');
  meuArquivo.print(q.x);
  meuArquivo.print(';');
  meuArquivo.print(q.y);
  meuArquivo.print(';');
  meuArquivo.print(q.z);
  meuArquivo.print(';');
  // Pressao
  meuArquivo.print(ValorPressao);
  meuArquivo.print(';');
  // Medição de Corrente
  meuArquivo.print(ValorMedCorr);
  meuArquivo.print(';');
  // Velocidade da Roda
  meuArquivo.print("0");
  meuArquivo.print(';');
  // Aceleração da aeronave
  meuArquivo.print(aaReal.x);
  meuArquivo.print(';');
  meuArquivo.print(aaReal.y);
  meuArquivo.print(';');
  meuArquivo.print(aaReal.z);
  meuArquivo.println();
}

void enviar_dados(){
  // Tempo
  Serial.print(tempo_inicio);
  Serial.print(';');
  // Pressao Diferencial
  Serial.print(long (ValorPrDif*100));
  Serial.print(';');
  // Orientação
  Serial.print(long (q.w*100));
  Serial.print(';');
  Serial.print(long (q.x*100));
  Serial.print(';');
  Serial.print(long (q.y*100));
  Serial.print(';');
  Serial.print(long (q.z*100));
  Serial.print(';');
  // Pressao
  Serial.print(ValorPressao);
  Serial.print(';');
  // Medição de Corrente
  Serial.print(ValorMedCorr);
  Serial.print(';');
  // Velocidade da Roda
  Serial.print(0);
  Serial.print(';');
  // Aceleração da aeronave
  Serial.print(aaReal.x);
  Serial.print(';');
  Serial.print(aaReal.y);
  Serial.print(';');
  Serial.print(aaReal.z);
  Serial.println(';');
}

void enviar_habilitados() {
  Serial.print(b_habilitado_cartao_sd);
  Serial.print(';');
  Serial.print(b_habilitado_orientacao_aceleracao);
  Serial.print(';');
  Serial.print(b_habilitado_pressao);
  Serial.print(';');
  Serial.print(b_habilitado_velocidade_roda);
  Serial.println(';');
}

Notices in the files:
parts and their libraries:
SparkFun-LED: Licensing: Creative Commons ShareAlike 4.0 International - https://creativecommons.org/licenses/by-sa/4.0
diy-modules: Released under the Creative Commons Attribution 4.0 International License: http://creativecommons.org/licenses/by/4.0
